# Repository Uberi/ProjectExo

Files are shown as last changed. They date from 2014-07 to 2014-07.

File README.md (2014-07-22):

Project Exo
===========
Design, schematics, and building instructions for a powered full-body exoskeleton.

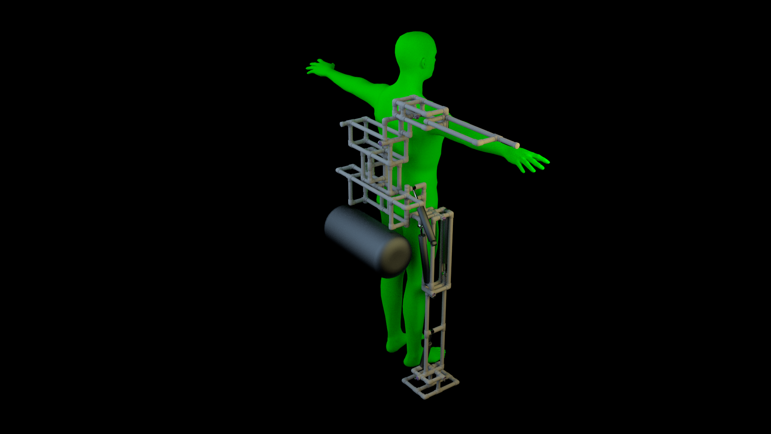
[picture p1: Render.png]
Render


Requires a basic understanding of math, usage of common power tools, and a fair bit of free time to build.

Total parts cost: \$810.48 CAD. ;wip: update this

Current Status
--------------

| Stage | Status | Time Needed (Approximate) |
|:---|:---|:---|
| Design Research | **Complete**  | 2 weeks |
| Design Requirements | **Complete**  | 4 days |
| Mechanical Design/Prototyping | 80% done | 4 weeks |
| Electronic Design/Prototyping | 10% done | 5 weeks |
| Part/Tool Sourcing | _Pending_ | 20 days |
| Production/Revision | _Pending_ | 4 weeks |

Estimated date of completion is **end of 2014**.

### To-Do:

* Finish design.
* Reduce amount of custom parts.
* Create a parts list.
* Write custom pneumatic piston controller with position and stiffness controls.
* Figure out where to get access to a CNC milling machine + machine shop.

Design
------

* One human operator (designed for height ~1.7m, but adjustable).
* Rigid, free-standing chassis made out of simple plumbing parts and common building materials, designed with large tolerances and excellent safety margins.
* Air tank stores compressed air for driving the pneumatic components.
* Sealed 12V lead-acid battery powers onboard electronics.
* Pressure sensitive armbands and legbands attached to chassis sense operator motion, which is fed into high-level control.
* Arduino driving a Darlington array provides high level control of all other subsystems.
* Electrically controlled 12V pneumatic valves control airflow to the pneumatic pistons.
* Pneumatic pistons move chassis.

Project Exo is designed to be easy to build, powerful, and as failsafe as possible. All parts operate well within their safety ratings, and plenty of care is taken to restrict the range of motion so that the actuators cannot harm the operator if they malfunction.

Files
-----

In order to view all the design files, you will need [Fritzing](http://fritzing.org/home/) and [Blender3D](http://www.blender.org/).

`Design/Design.blend` contains a Blender3D CAD file for the entire system. ;wip: add this to the Git repo
`Design/High Level Controller` contains a Fritzing schematic for the high level pneumatics controller.

Tools
-----

* Metal/plastic saw
* Soldering iron
* Standard epoxy
* Hot glue gun + hot glue
* Screwdriver
* Pliers
* Scissors

A Dremel is also always a nice thing to have on hand. Not strictly necessary, but highly recommended.

Mechanical Parts
----------------

The mechanical parts list can be broken down as follows:

| Part | Quantity | Market Price (CAD) |
|:---|:---|---:|
| Pipes and pipe joints/connectors | A lot | 50.00 | ;wip: not an exact value
| Double action pneumatic pistons  | 6 short, 2 small, 4 large | 103.44 + 22.08 + 112.84 |
| Pneumatic regulators | 3 | 52.50 |
| Pneumatic valves | 24 | 177.60 |
| Air tank | 1 | 59.99 |
| Battery | 1 | 27.49 |
| PVC primer + cement | 500ml | 19.98
| Pneumatic accessories | 1 compressor, 1 filter | 137.09 + 19.99 |

In total, the current market price of the mechanical parts is \$783 CAD.

### Pipes and Pipe Joints/Connectors

I will be using 2cm outer diameter PVC piping, but any similar diameter will work - the tolerances are reasonably loose. The diameter should be at least 1.5cm to ensure the frame is strong enough. Use schedule 80 piping if possible - it has thicker pipe walls and is therefore stronger.

The chassis is constructed mostly out of pipes and joints, so the strength of the frame is significantly affected by how strong the pipes and joints are.

Pipes and pipe joints/connectors should be available at almost any [hardware store](http://homehardware.ca/en/rec/index.htm/Plumbing-Electrical/Plumbing/Waterworks/Water-Pipes/Pvc/1-1-4-x-10-PVC-Pressure-Pipe/_/N-2pqfZ67l/Ne-67n/Ntk-All_EN/R-I326206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). Failing that, see [Amazon](http://www.amazon.com/Charlotte-Pipe-PVC-04010-0200/dp/B003OSSDWW/) or similar.

Metal pipes would make the whole frame stronger, but the tools for working with them are harder to obtain.

Pipe joints include things like elbow joints, tee joints, and more obscure ones like vee joints. These are optional if using metal pipes and welding them together.

The design files includes some "unconventional" pipe fittings such as four way and corner fittings, which are generally not available in stores due to not being very useful for plumbing purposes. These fittings can instead be obtained from specialty PVC construction suppliers:

* [Formufit](http://www.formufit.com/), in addition to selling all of the types of PVC components needed for this project, offers guides and tutorials for working with PVC.
    * A little bit more expensive but very good quality.
    * The products are also sold on [Amazon](http://www.amazon.com/gp/aag/main?ie=UTF8marketplaceID=ATVPDKIKX0DER&seller=A1T0WSE1JGO9PT).
* [PVC Plans](http://www.pvcplans.com/pvc-suppliers.htm) maintains a list of suppliers, many of which offer these non-standard fittings.
    * USA-centric, but several will ship internationally. Sellers seem reputable.
* [PVC Fittings](http://pvcfittings.com/) offers the lowest prices 
    * Ridiculously large variety of parts available, but shipping options are limited.

### Double Action Pneumatic Pistons

I will be using [MAL 16 X 175 Double Action Pneumatic Pistons](http://www.ebay.com/itm/1Pcs-Single-Rod-16-x-175-Dual-Action-Mini-Pneumatic-Cylinder-/141094409413) (16mm bore, 175mm stroke) as the small pistons.

I will be using [MAL 32 X 175 Double Action Pneumatic Pistons](http://www.ebay.com/itm/32mm-Bore-175mm-Stroke-Double-Action-Aluminum-Alloy-Pneumatic-Air-Cylinder-/310973376044) (32mm bore, 175mm stroke) as the large pistons.

;wip: almost out of stock, maybe http://www.ebay.com/itm/MA32-175S-CM-Mini-Pneumatic-Cylinder-Double-Acting-32-175mm-AIRTAC-Type-/261362580432 or http://www.ebay.com/itm/AIRTAC-Type-MA32-175S-CM-Mini-Pneumatic-Cylinder-Double-Acting-32-175mm-/171175049747 instead

I will be using [CQ2B32-100D Double Action Pneumatic Pistons](http://www.ebay.com/itm/General-Model-CQ2B32-100D-Compact-Cylinder-Double-Acting-32-100mm-/360898853102) (32mm bore, 100mm stroke) as the short pistons.

The exact bore and stroke length isn't that important as long as it outputs enough force and still fits inside the frame.

The pistons are responsible for actually moving the frame, and the operator inside of it, around.

The bore is the diameter of the hole in which the plunger can move back and forth.

It is very important that the pistons are double action. This means that they can push out and pull in - single action cylinders can only do one of these.

The amount of force the piston can output is (essentially) proportional to the surface area of the plunger head, so $F = 0.006895 \pi \frac{d^2}{4} p$, where $F$ is the force in Newtons (9.8 Newtons is roughly 1kg in Earth gravity), $d$ is the bore diameter in mm, and $p$ is the pressure in psi.

So to be able to lift 10kg with a pressure of 100psi, we have $9.8 \times 10kg = 0.006895 \pi d^2 100$, so $d = \sqrt{\frac{9.8 \times 10}{0.006895 \frac 1 4 \pi 100}} \approxeq 13.5$. So we need a bore of at least around 14mm to do the lifting.

The stroke length is very important as well. This is the length that the piston can extend from rest position - the length of the path the piston can extend along. If the stroke is not long enough, the range of motion of some of the joints may be restricted. If the stroke is too long, it is possible to bend the joints too far, which could be a safety concern if there is a malfunction.

### Pneumatic Regulators

I will be using [4214-ADJ 1/4" Male-to-Female Pressure Regulators](http://www.amazon.com/Coilhose-Pneumatics-4214-ADJ-Adjustable-Regulator/dp/B0037QFFT0/), which are rated for 150psi max input pressure and output between 50psi and 145psi.

;wip: possibly http://www.amazon.com/Mini-Pressure-Regulator-Free-Gauge/dp/B004VGA7NY/ instead, it's cheaper

Pneumatic regulators are very important for safety purposes - they output gas at a constant pressure, even if the input pressure goes over.

### Pneumatic Valves

I will be using [1/2" Normally Closed 12V Solenoid Air Valves](http://www.ebay.com/itm/Electric-Solenoid-Valve-For-Water-Air-N-C-12V-DC-1-2-Normally-Closed-/370725933898), which are normally closed and rated at 116psi and continuous duty. When activated, they draw about 250mA.

Pneumatic air valves control airflows using electrical signals. This allows us to control the pneumatic actuators from the electrical systems.

### Air Tank

I will be using a [DSBP99210-2 2 gallon air tank](http://www.amazon.com/Smittybilt-99210-2-Gloss-Gallon-Fittings/dp/B003EP2XA8/) rated for 150psi.

The air tank stores the compressed air that drives the pneumatic actuators.

### Battery

I will be using a [UT1270 12V Sealed Lead-Acid Battery](http://www.amazon.ca/UltraTech-UT1270-Sealed-Battery-UT-1270/dp/B00BMUV2VS/), which is rated at 7Ah. It is also worth getting a [12V battery charger](http://www.amazon.com/gp/product/B004EI6A8K/) to go with it.

For testing purposes, it might also be useful to have a [12V Wall Power Supply](http://www.amazon.ca/Quality-Supply-Adapter-Converter-100-240V/dp/B00HSW3X3O/) for testing purposes.

### PVC Primer + Cement

I will be using [Oatley 30755 PVC Primer/Cleaner](http://www.amazon.ca/Oatey-30755-Purple-Primer-Fittings/dp/B00002N6NV/) and [Oatley 30883 PVC Cement](http://www.amazon.ca/Oatey-30883-Medium-Cement-Misc/dp/B000KGB2MO/) for PVC joining.

PVC cement joins PVC by reacting with the two surfaces to join and chemically bonding them together. Out of the factory, PVC is coated with various other material, which must be removed using PVC primer.

The resulting bond has high structural strength, and the joined piece can be load bearing.

### Pneumatic Accessories

An air compressor is very useful for refilling the air tank. I will be using a [VIAIR 300P Portable Air Compressor](http://www.amazon.ca/VIAIR-30033-300P-Portable-Compressor/dp/B000X90YUO/), which is rated for 150psi max.

;wip: also consider http://www.amazon.com/VIAIR-150-PSI-High-Flow-Source/dp/B000X9LTXA/ to replace the compressor and air tank

An air filter helps remove moisture and dust, in order to keep the system clean over extended use. I will be using a [F1401 1/4" 40 Micron Air Filter](http://www.amazon.com/Primefit-F1401-Filter-60-SCFM-100-PSI/dp/B00IDCYIPK/), which are rated for 145psi max.

Electronic Parts
----------------

The electronic parts list can be broken down as follows:

| Part | Quantity | Market Price (CAD) | Vendor |
|:---|:---|---:|:---|
| P120PK potentiometer | 12 | 9.48 | [Digi-Key](http://www.digikey.ca/product-search/en?keywords=P120PK) |
| Arduino Nano revision 3 | 1 | 18.00 | [Amazon](http://www.amazon.ca/SainSmart-Nano-v3-0-Compatible-Arduino/dp/B00761NDHI/) |
| 4-channel 1.5A Darlington array  | 6 | 18.12 | [Digi-Key](http://www.digikey.ca/product-detail/en/ULN2069B/497-2352-5-ND/599589) |
;wip: pressure switches, perfboard, etc.

In total, the current market price of the mechanical parts is \$27.48 CAD. ;wip: update this

Electronic parts are a bit more fickle than the mechanical ones, since there are so many factors to consider that suggesting substitutes and alternatives would be impractical. I will be using the exact parts specified.

Building
--------

DISCLAIMER: Compressed air, electricity, and power tools can be dangerous if you're not careful. I am not responsible for any death, dismemberment, spontaneous defecation, or hair loss that may result from following the instructions in this document.

;wip

License
-------

<br /><span xmlns:dct="http://purl.org/dc/terms/" property="dct:title">Project Exo</span> by <a xmlns:cc="http://creativecommons.org/ns#" href="https://github.com/Uberi/ProjectExo" property="cc:attributionName" rel="cc:attributionURL">Anthony Zhang</a> is licensed under a <a rel="license" href="http://creativecommons.org/licenses/by-nc-sa/4.0/">Creative Commons Attribution-NonCommercial-ShareAlike 4.0 International License</a>.

    THE SOFTWARE IS PROVIDED "AS IS", WITHOUT WARRANTY OF ANY KIND, EXPRESS OR
    IMPLIED, INCLUDING BUT NOT LIMITED TO THE WARRANTIES OF MERCHANTABILITY,
    FITNESS FOR A PARTICULAR PURPOSE AND NONINFRINGEMENT. IN NO EVENT SHALL THE
    AUTHORS OR COPYRIGHT HOLDERS BE LIABLE FOR ANY CLAIM, DAMAGES OR OTHER
    LIABILITY, WHETHER IN AN ACTION OF CONTRACT, TORT OR OTHERWISE, ARISING FROM,
    OUT OF OR IN CONNECTION WITH THE SOFTWARE OR THE USE OR OTHER DEALINGS IN
    THE SOFTWARE.

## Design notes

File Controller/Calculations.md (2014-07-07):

Pneumatic Limb Controller
-------------------------

$$
\newcommand{\dee}{\mathop{}\!\mathrm{d}}
$$

Strength Capabilities
---------------------

* $P_1$ is the pressure on the near side of the plunger (Newtons per square meter).
* $P_2$ is the pressure on the far side of the plunger (Newtons per square meter).
* $D$ is the bore (diameter) of the pneumatic piston (meters).

The force acting on the piston plunger is $(P_1 - P_2)\pi\left(\frac D 2 \right)^2$.

With $P_1, P_2$ in PSI and $D$ in millimeters, we have $P_1 \mathrm{lbf}/(25.4 \mathrm{mm})^2 \pi\left(\frac {D \mathrm{mm}} 2 \right)^2 \approxeq 0.001217369588005(P_1 - P_2)D^2$.

So if we have 100psi on one end and 0psi on the other of a 32mm bore piston, the force is $0.001217369588005(100 - 0)32^2$, or $124.658645811712$ pounds-force. That means it would be able to lift a 124 pound weight directly upwards.

Of course, the actual force exerted by the limbs is less than this due to limb leverage. For example, the knee joint in the design has a roughly 1:6 mechanical advantage, which means that we would actually be able to lift a 21 pound weight directly upwards.

Pneumatic Controller
--------------------

* $P_1$ is the pressure on the near side of the plunger (Newtons per square meter).
* $P_2$ is the pressure on the far side of the plunger (Newtons per square meter).
* $x$ is the extension of the piston (meters).
* $\theta$ is the rotation of the limb (radians).
* $L$ is the length of the limb (meters).
* $s$ is the distance between the limb and the piston (meters).

We want a function $f(\theta')$ that accepts a target position and results in the amount to set $P_1 - P_2$ to to ensure $\theta$ converges toward $\theta'$ quickly.

Let $k$ be the surface area of the piston plunger. Then $\frac{\dee^2 x}{\dee t^2} = k(P_1 - P_2) + F$.

By the cosine law, $x^2 = s^2 + L^2 - 2sL \cos \theta$ and $x = \sqrt{s^2 + L^2 - 2sL \cos \theta}$.

The accuracy of $\cos$ is $\pm 0.001$ in the output, so $x = \sqrt{s^2 + L^2 - 2sL \cos \theta \pm 0.002sL}$.

The pneumatic controller uses this to convert the setpoint and measured value of a PID controller so that it works in terms of $x$ rather than $\theta$. The PID controller then calculates the value of $P_1 - P_2$.

Also, $\theta = \arccos \frac{s^2 + L^2 - x^2}{2sL}$.

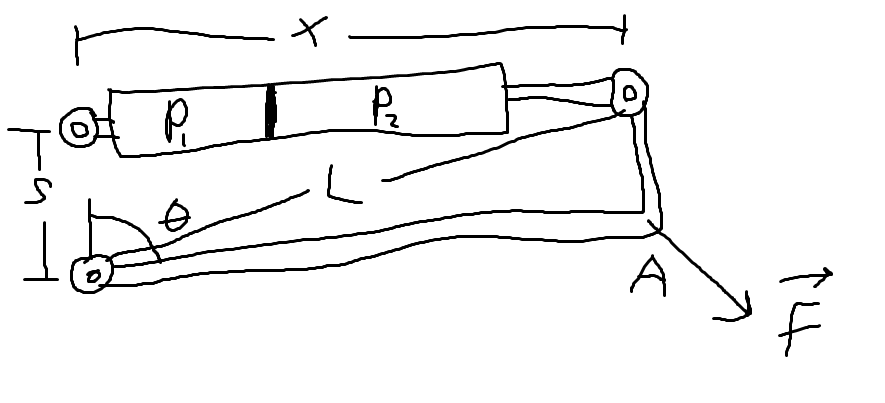
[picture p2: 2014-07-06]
Controller/Diagram.png

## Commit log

2014-06-29 Add standard form PID controller, update README, create basic high-level controller.
    [High Level Controller.fzz, Motor Driver Arduino.fzz]
2014-07-06 Add PID-powered limb controller library, upgrade PID controller with low-pass filter on derivative term, explain some of the calculations, add PVC working guides in reference section.
2014-08-01 Account for velocity in Limb controller.
